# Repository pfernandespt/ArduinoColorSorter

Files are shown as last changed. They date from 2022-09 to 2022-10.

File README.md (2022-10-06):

# ArduinoColorSorter
## Introdução
Todo este trabalho tem origem no projeto a desenvolver proposto pelo professor da UC de Introdução à Engenharia Eletrotécnica.
Todos os diferentes projetos sugeridos tinham a sua base na plataforma Arduino com objetivos de trabalho diferentes.

Foi-nos proposto o desenvolvimento de um projeto que tivesse por base o controlo de posição e velocidade síncrono de 2 motores passo Nema17 usando drivers controladores L293D, contidos num módulo shield para um Arduino UNO.

Depois de alguma troca de ideias pensamos em fazer um dispositivo capaz de identificar a cor de um objeto e com base nisso separá-lo junto com outros de uma cor semelhante, ou seja, um separador de objetos por cor, uma vez que seria basicamente necessário adicionar um sensor de cor ao projeto. Decidimos adicionar também um botão para pausar/resumir o programa e uma fita de LEDs para uma fácil visualização da cor do objeto identificada pelo sensor.

Depois de alguma pesquisa percebemos que o uma boa opção seriam M&M’s: fáceis de obter, tendo 6 cores diferentes (vermelho, laranja, amarelo, verde, azul e castanho) e tamanhos semelhantes entre si.

O nosso projeto teve inspiração em alguns trabalhos anteriores que encontramos através de pesquisa na internet. O mais relevante terá sido um projeto completo desenvolvido por Willem Pennings muito bem documentado, com imagens e com projeto também no github:
 - [M&Ms and Skittles sorting machine](https://willempennings.nl/mms-and-skittles-sorting-machine/)
 - [Projeto GitHub](https://github.com/willem-pennings/Candy-sorting-machine)

## Material
  - 1 arduino
  - 1 módulo Adafruit Motor Shield;
  - 2 motores stepper/passo Nema 17;
  - 1 sensor de cor TCS34725 da DFRobot;
  - 1 fita de LEDs digital/endereçável de 1m, com 60LEDs/m;
  - 1 botão
  - x fios de ligação (jumpers)
  
## Hardware
  #### Esquema de Montagem (Schematic)
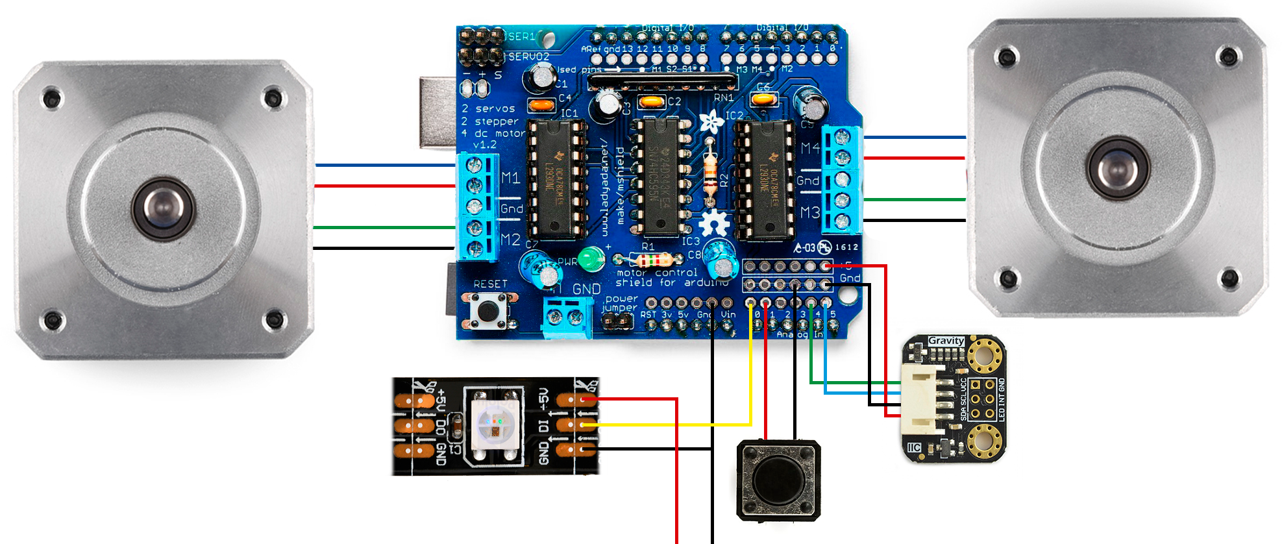
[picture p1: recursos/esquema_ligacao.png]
schematic
  
  
  #### Parte Mecânica
  Para facilitar o manuseamento dos M&M’s decidimos imprimir algumas peças em 3D:
  A peça amarela é da autoria de Willem Pennings retirada do projeto mencionado acima e as outras duas foram modeladas por nós no software Fusion 360.
  
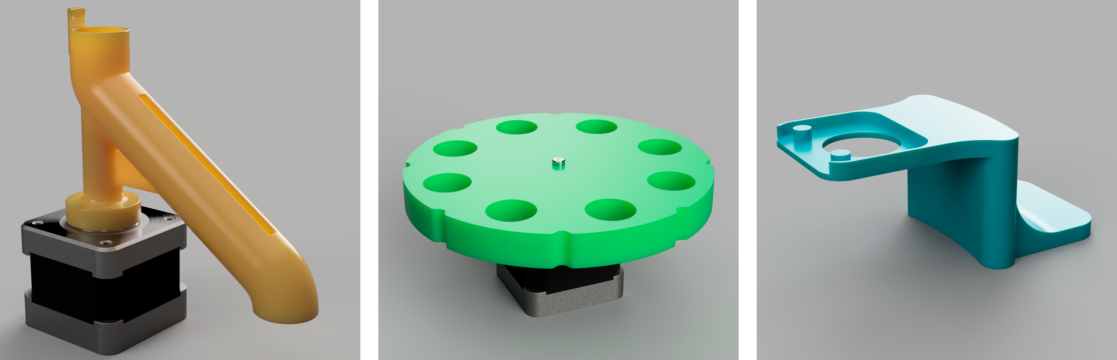
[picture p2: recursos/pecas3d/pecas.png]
pecas
  
  
  O motor com a peça amarela acoplada funciona como o próprio seletor do recipiente adequado, a verde é aquela que move os objetos sucessivamente até ao sensor e ao seletor (amarelo). Já a peça azul funciona como um suporte para o sensor de cor para que as leituras sejam mais consistentes à distância ideal.
  
  #### Prototipo Final
  
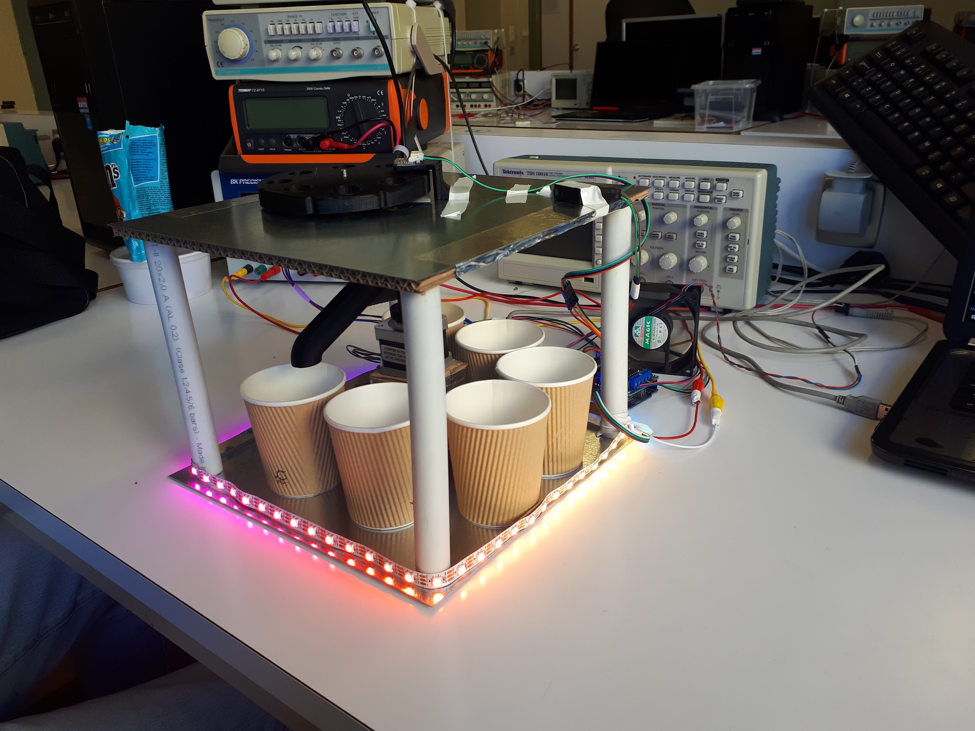
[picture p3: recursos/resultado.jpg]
prototype
  
  
  A ideia inicial era de fazer a estrutura redonda em MDF cortado a laser (como no modelo 3D), mas acabamos por fazer um modelo retangular de cartão e chapa galvanizada para lhe conferir resistência (acima).
  
## Software
#### Explicação
Todo o software foi desenvolvido e aperfeiçoado por nós, tendo tido por base algumas bibliotecas:
  - Wire.h (comunicação Arduino - Sensor Cor)
  - DFRobot_TCS34725.h (comunicação Arduino - Sensor Cor)
  - AFMotor.h (controlo dos motores stepper com o shield AdaFruit)
  - FastLED.h (controlo dos LEDs digitais)
Depois de procurar códigos de dispositivos como este online para inspiração decidimos desenvolver um método mais simples que aqueles que encontrámos na determinação da cor de cada objeto. 

Em vez de fazer comparações de cada um dos parâmetros R, G e B da cor lida pelo sensor com valores padrão pensamos no seguinte método:
  1. Construir pontos no espaço cujas coordenadas sejam os valores R,G e B das cores lida e
padrão (Ex: R:255 G:125 B:0 forma o ponto S de coordenadas (255, 125, 0));
  2. Calcular a distância entre o ponto correspondente à cor lida e cada um dos pontos
correspondentes aos valores padrão;
  3. Determinar a distância mínima das anteriores;
  4. Deduzir qual o ponto mais próximo ao lido e, como consequência, determinar a cor mais
próxima.

O processo descrito acima pode ser vizualizado com a ajuda do seguinte gráfico:
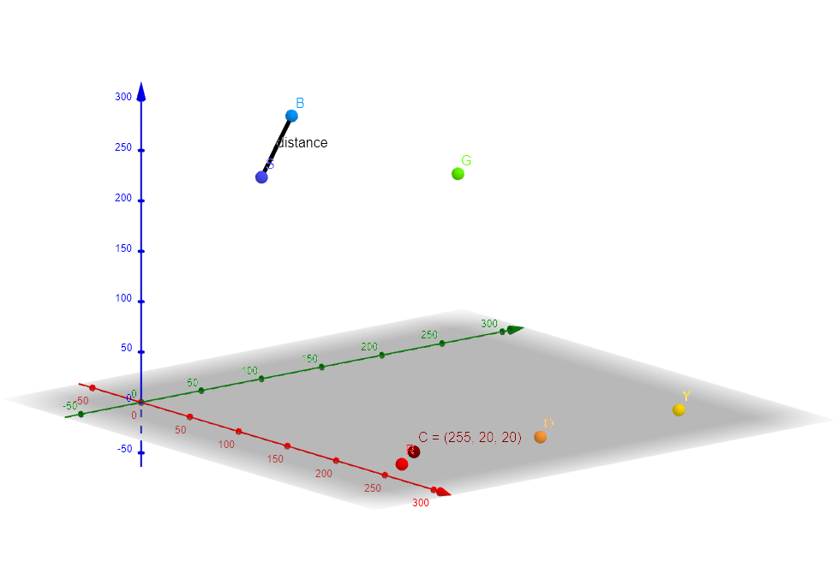
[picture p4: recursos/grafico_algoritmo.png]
explanation_diagram

Aqui é feita uma abstração dos eixos x, y e z aos valores R, G e B das cores lidas.

#### Código Responsável

Aproximação da cor:
```c
  int aprox_color(){ //devolve o numero da cor mais proxima a que foi lida no sensor
	int color_number = 0;
	float min_distance = distance(0);
  for(int i = 0; i < 7; ++i){
    float cur_distance = distance(i);
    if(cur_distance < min_distance){
      color_number = i;
      min_distance = cur_distance;
    }
  }
  return color_number;
}
```
```c
float distance(int i){ // calcula a distancia da cor lida a cor indicada no argumento
  float dist = sqrt(pow((r-cor[i].r),2) + pow((g-cor[i].g),2) + pow((b-cor[i].b),2));
  return dist;
}
```

Movimento dos motores:
```c
void move2(){
  int movement = abs(next_pos - last_pos);
  movement *= sector_amplitude;
  Serial.print("movimento motor baixo:");
  Serial.println(movement);
  if(next_pos > last_pos) {
    motor2.step(movement, FORWARD, DOUBLE);
    delay(100);
  }
  else {
    motor2.step(movement, BACKWARD, DOUBLE);
    delay(100);
  }
  
  last_pos = next_pos;
}
```

Para informação mais detalhada acerca deste projeto, por favor, consultar os documentos produzidos: [Relatório e Powerpoint](documentos)

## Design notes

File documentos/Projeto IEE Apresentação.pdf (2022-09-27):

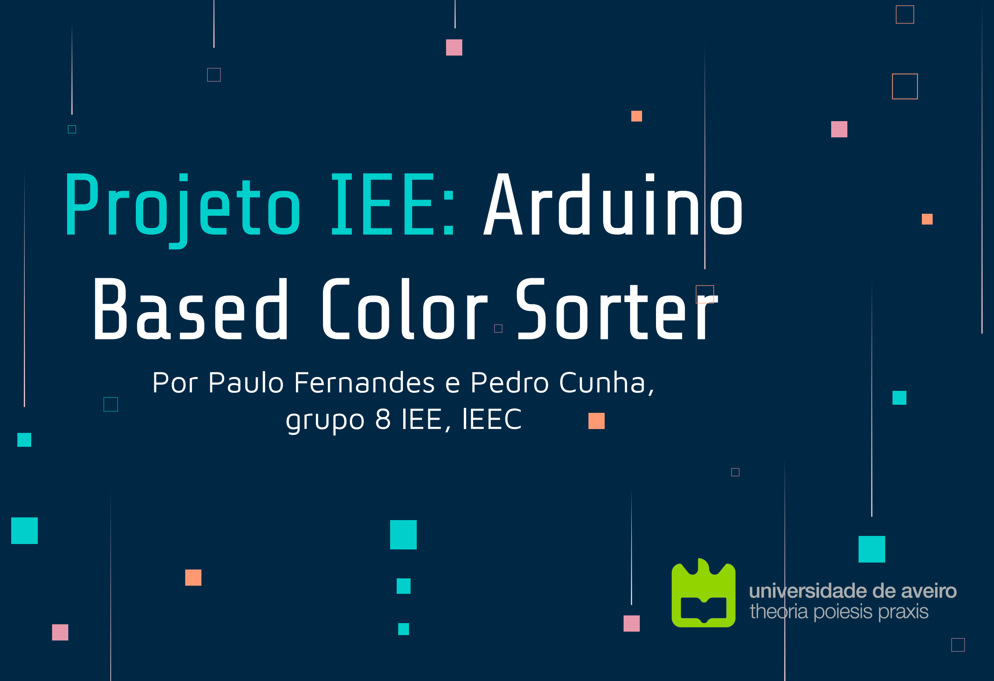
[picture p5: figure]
Por Paulo Fernandes e Pedro Cunha, grupo 8 IEE, lEEC; Projeto IEE: Arduino Based Color Sorter

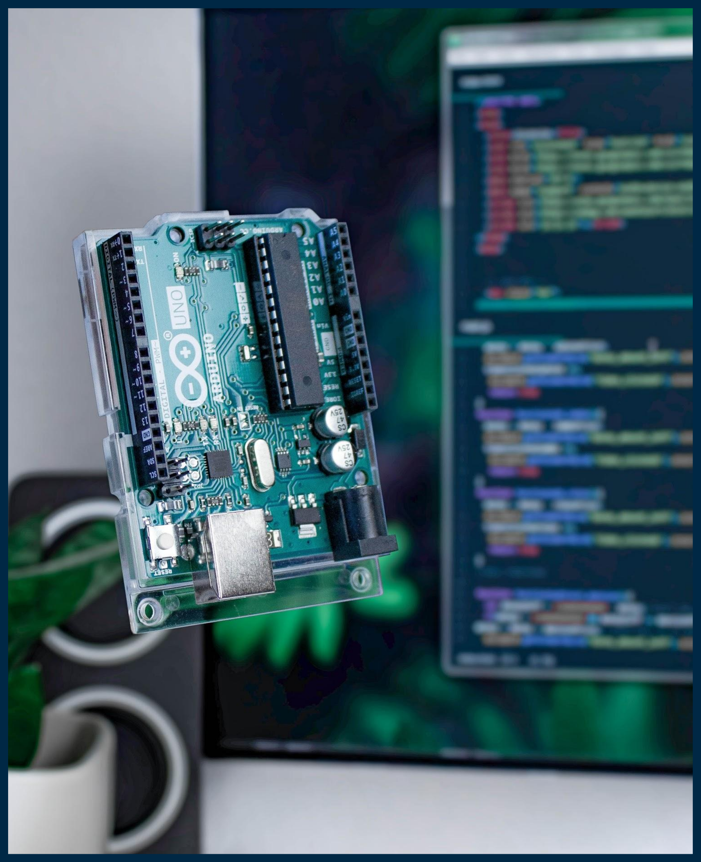
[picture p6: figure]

1. Plataforma Arduino;
2. Ideia base do Projeto;
3. Complementos;
4. Projeto como um todo;
5. Esquema de ligação;
6. Esquema de funcionamento;
7. Código;
8. Resultado;
9. Possíveis aplicações.

## Índice

O Arduino é uma plataforma open-source baseada em hardware e software de fácil manipulação. As placas Arduino são capazes de ler entradas e torná-las em saídas, seja através de sinais analógicos ou digitais. Tudo isto é feito através de uma linguagem de Programação baseada em C. (Adaptado de: What is Arduino?, arduino.cc) (https://www.arduino.cc/en/Guide/Introduction)

## Plataforma Arduino

Materiais Base:
■ 2 Motores stepper Nema17;
■ Adafruit Shield controlador de motores stepper para Arduino; ■ Arduino.

Objetivo: Desenvolvimento de um programa capaz de controlar velocidade e posição de motores stepper Nema17 aplicada a um trabalho e tendo por base os controladores L239D.

## Ideia Base do Projeto

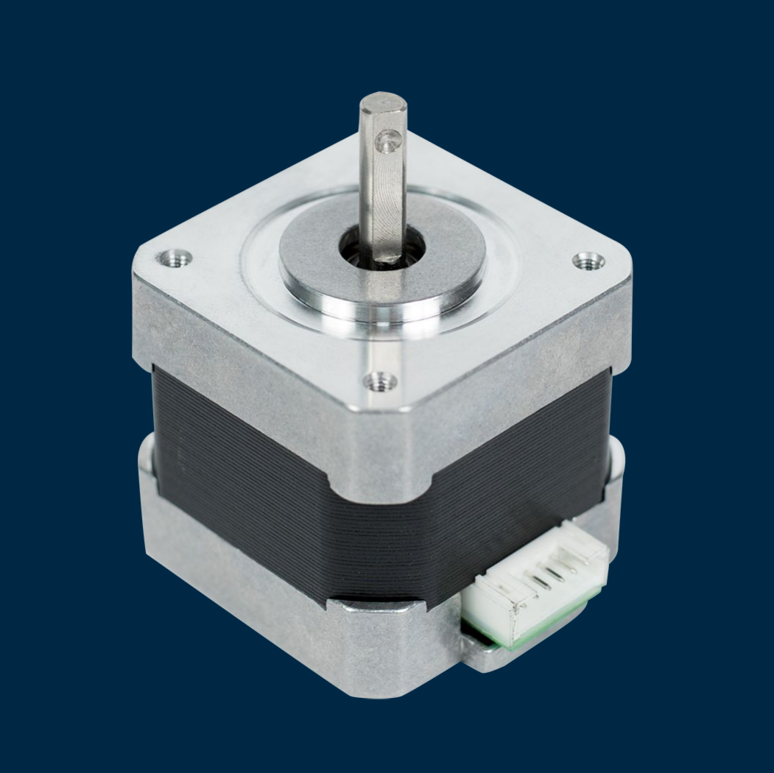
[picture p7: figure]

Desc.: Motor de passo bipolar

Características:
■ Número de fases: 2 (4 fios)
■ Passos por volta: 200
■ Ângulo de passo: 1.8º
■ Tensões de funcionamento: 5-12V

## Motores Stepper Nema17

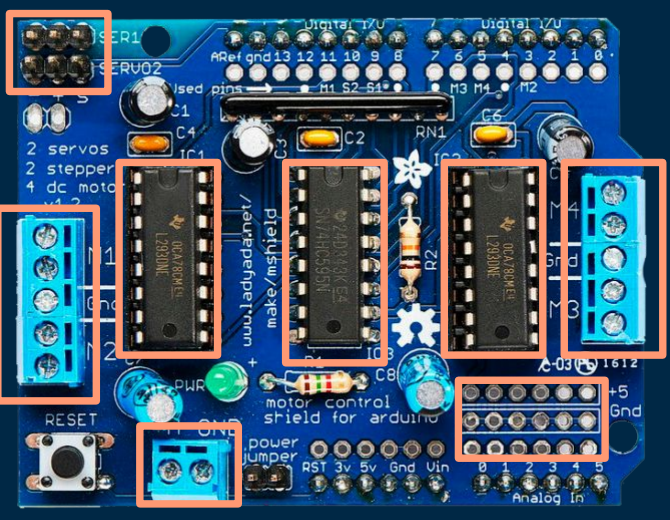
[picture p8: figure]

Desc.: “Shield” para Arduino que permite controlar diferentes tipos de motores (4 DC, 2 Stepper, 2 Servo).

Características:
■ 2 Drivers L293D
■ Fácil instalação no Arduino
■ Deixa livres as portas Analógicas do Arduino

## Adafruit Motor Shield

A nossa ideia de projeto implicou que fossem usados mais dispositivos eletrónicos:
■ Sensor de cor RGB DFRobot TCS34725
■ Fita de LEDs digital WS2812B 60LED/m
■ Botão Push
■ Jumpers

## Complementos

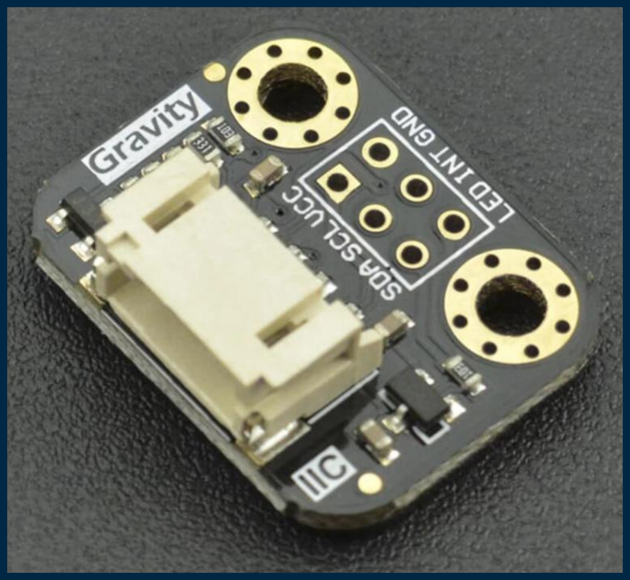
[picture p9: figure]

Desc.:Sensor de cor que permite obter os valores R, G e B de um objeto colocado na sua frente

Características:
■ Possui LEDs para melhor leitura ■ Padrão de comunicação: I2C ■ Usa apenas 2 Portas Analógicas

## Sensor de Cor RGB TCS34725

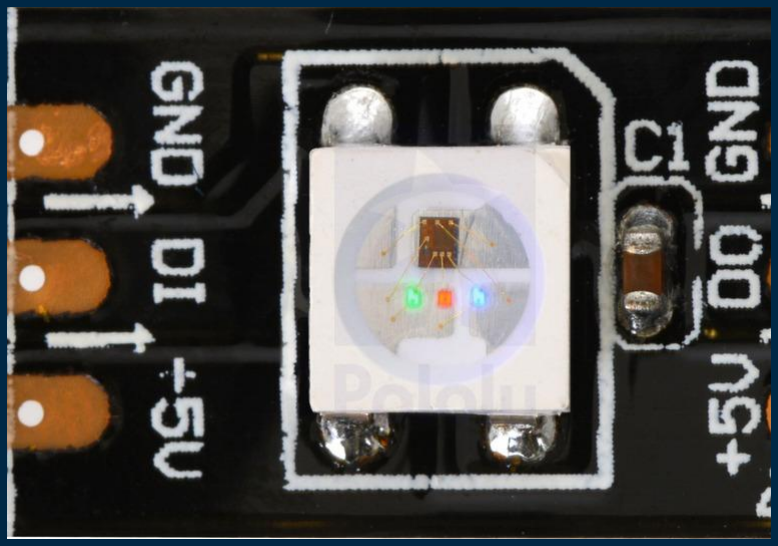
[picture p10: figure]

Desc.: Fita de LEDs endereçáveis de “baixo” consumo que exibe cores de 8 bits.

Características:
■ Potência máxima: 18W
■ Digital (controlo com 1 pino)

## Fita de LEDs WS2812B

Ideia principal do projeto: criação de um dispositivo capaz de separar objetos de cores diferentes.

Objeto a separar: M&M’s
■ Boa dimensão para fins demonstrativos
■ 6 cores: Vermelho, Laranja, Amarelo, Verde, Azul e Castanho ■ Tamanho consistente

## Projeto

## Projeto

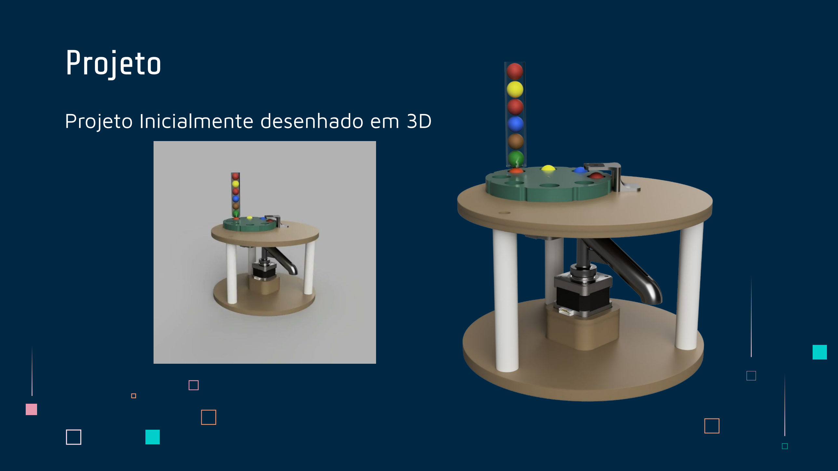
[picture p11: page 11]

Projeto Inicialmente desenhado em 3D

## Esquema de Ligação

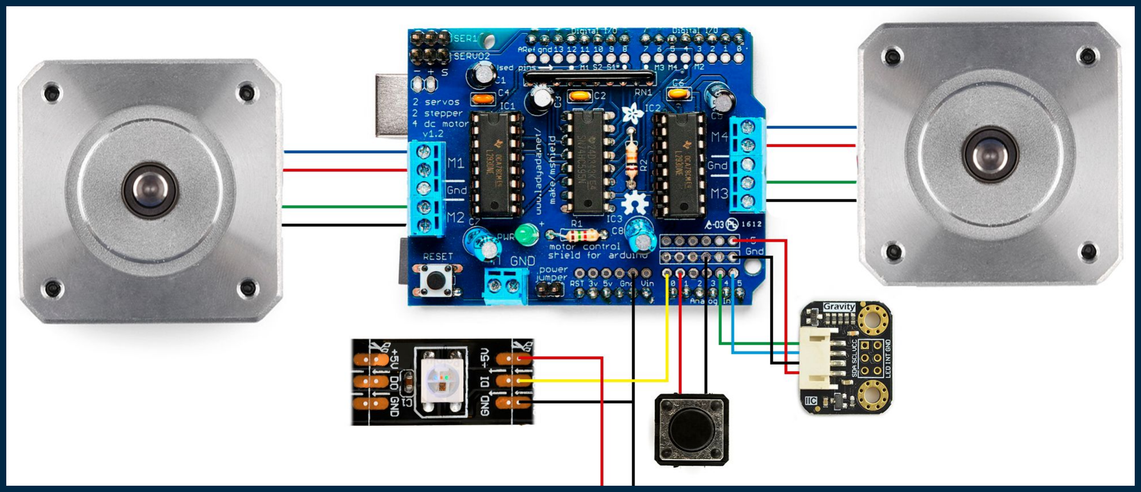
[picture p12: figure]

## Esquema de funcionamento

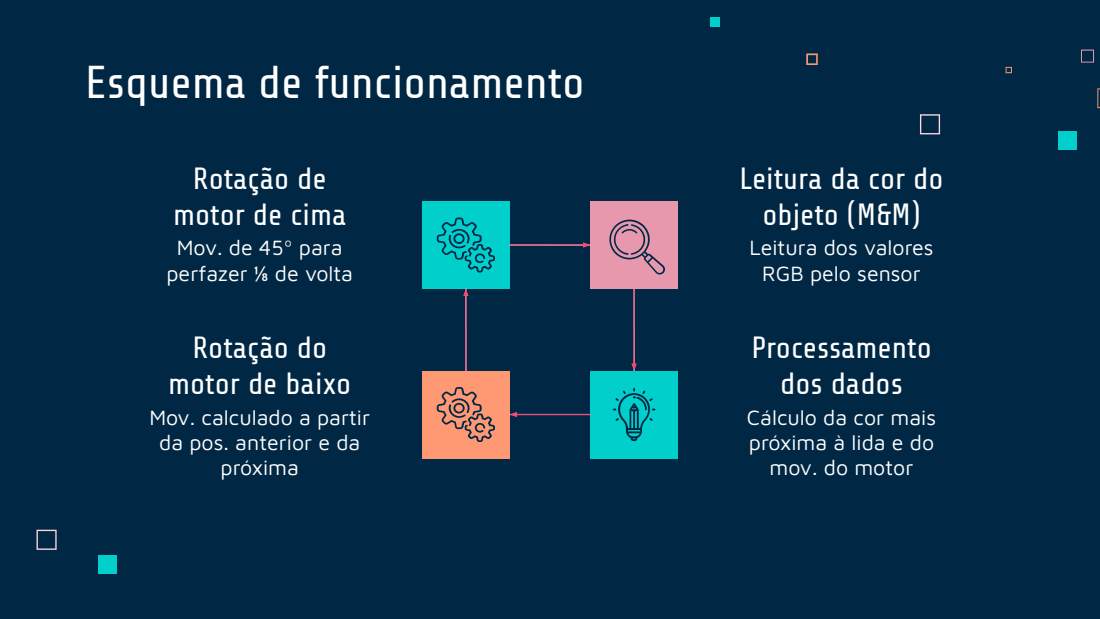
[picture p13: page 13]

Rotação de
motor de cima
Mov. de 45º para
perfazer ⅛ de volta

Leitura da cor do
objeto (M&M)
Leitura dos valores
RGB pelo sensor

Rotação do
motor de baixo
Mov. calculado a partir
da pos. anterior e da
próxima

Processamento
dos dados
Cálculo da cor mais
próxima à lida e do
mov. do motor

## Código (Processamento dos dados)

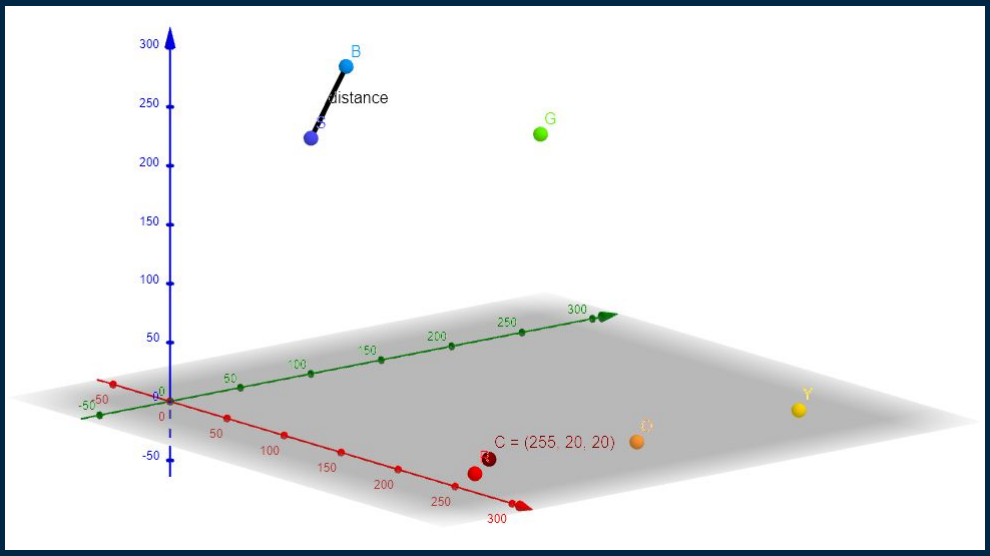
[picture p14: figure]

# Resultado

## Possíveis aplicações

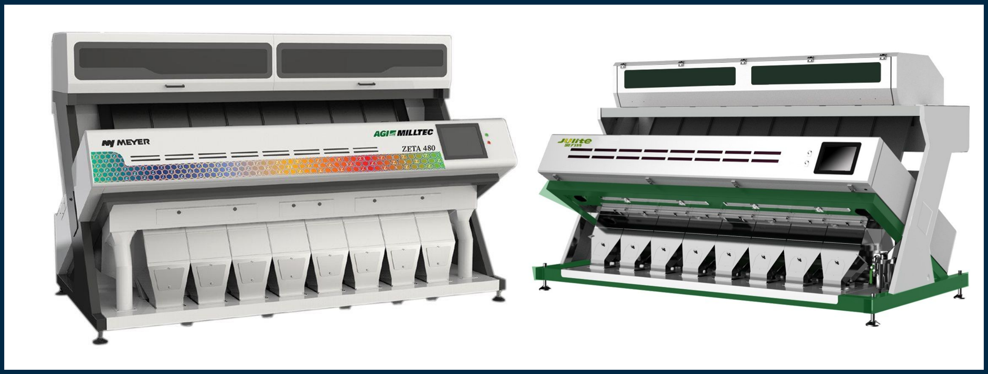
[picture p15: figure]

Indústria alimentícia no processamento de: ■ Milho
■ Feijão
■ Trigo
■ Sesamo
■ Arroz
■ Amendoins
■ Frutas

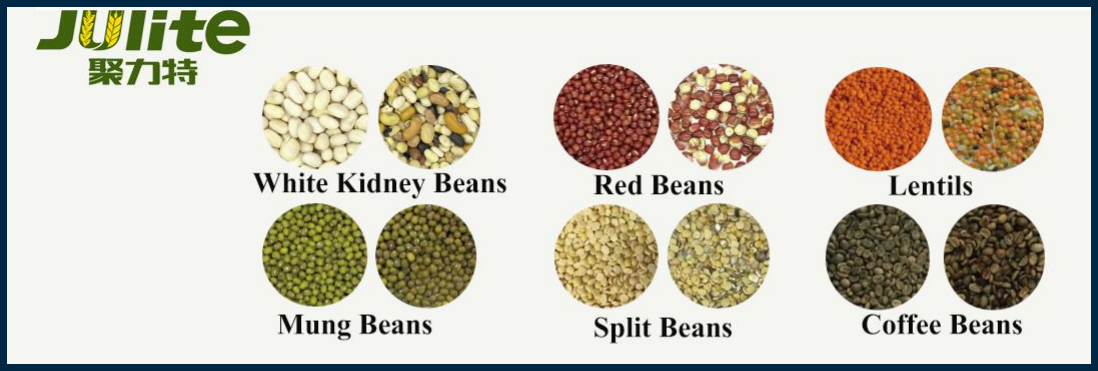
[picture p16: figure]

■ Sementes de Girassol
■ Outros…

## Possíveis aplicações

Separação de plásticos para reciclagem

## Possíveis aplicações

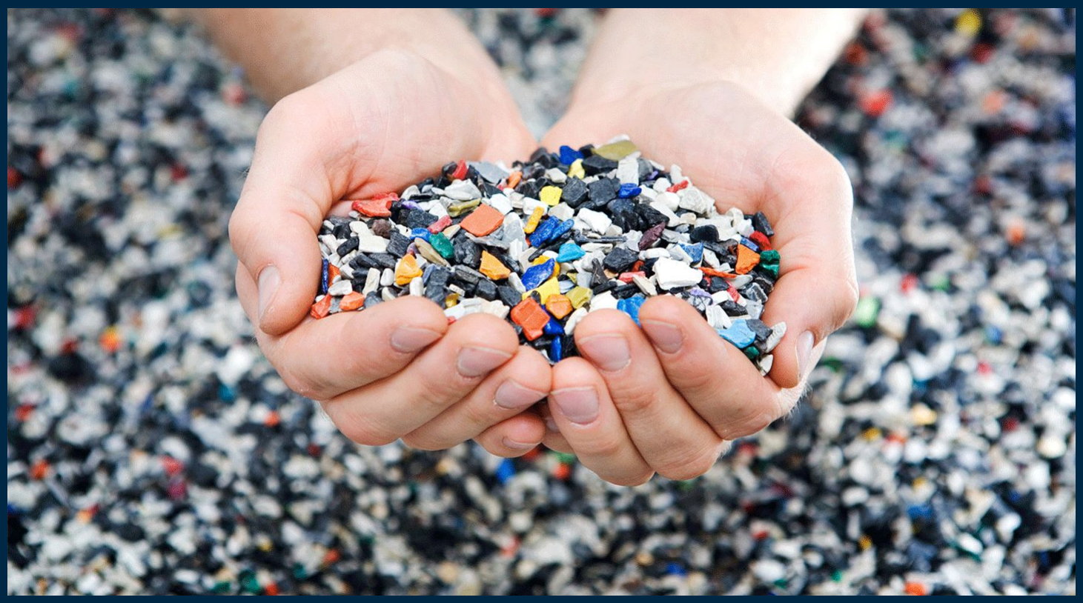
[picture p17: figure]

# Obrigado!

■ Arduino - What is Arduino (https://www.arduino.cc/en/Guide/Introduction)
■ LastMinuteEnginieers - Motor Shield (https://lastminuteengineers.com/l293d-motor-driver-shield-arduino-tutorial/)
■ CircuitBasics - Basics of the I2C communication protocol (https://www.circuitbasics.com/basics-of-the-i2c-communication-protocol/) ■ Julite - Color Sorter (https://www.julite.com/Product/id/236.html)

## Fontes

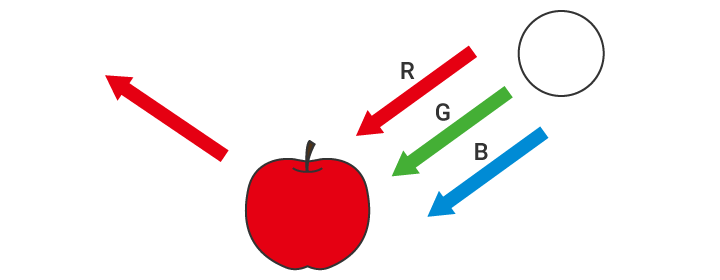
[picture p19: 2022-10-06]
recursos/sensor_cor1.png

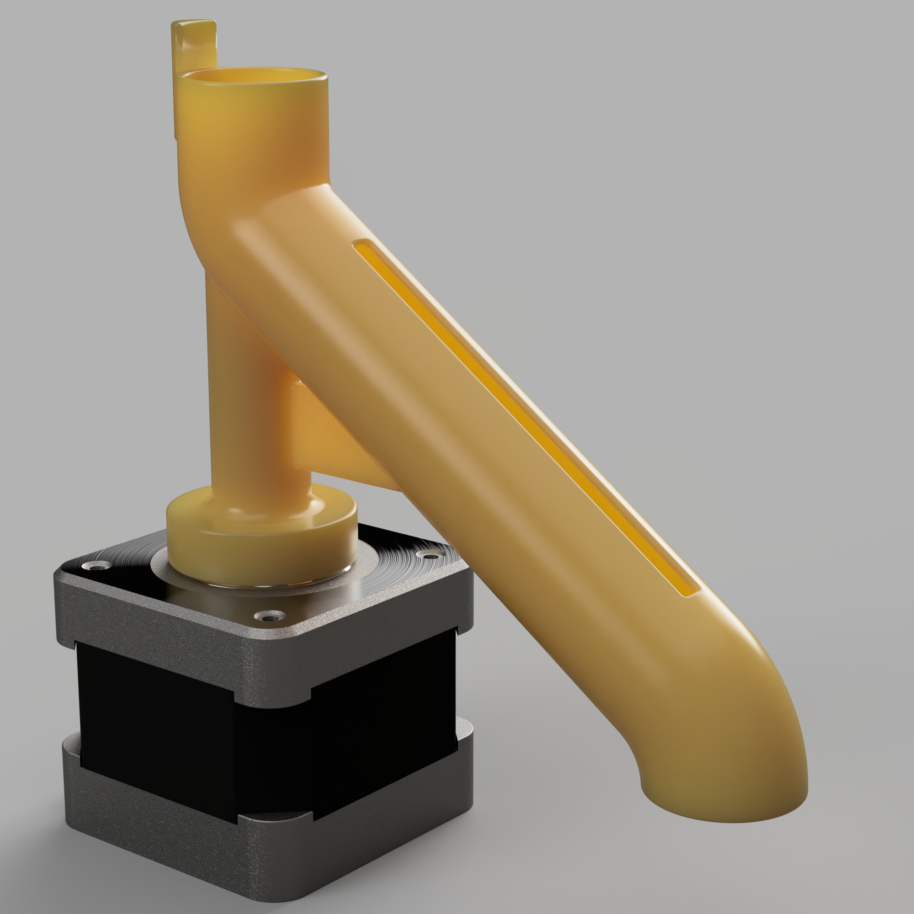
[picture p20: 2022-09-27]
recursos/pecas3d/peca1.png

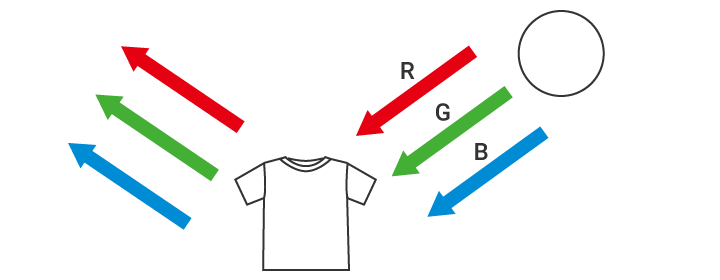
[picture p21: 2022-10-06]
recursos/sensor_cor2.png

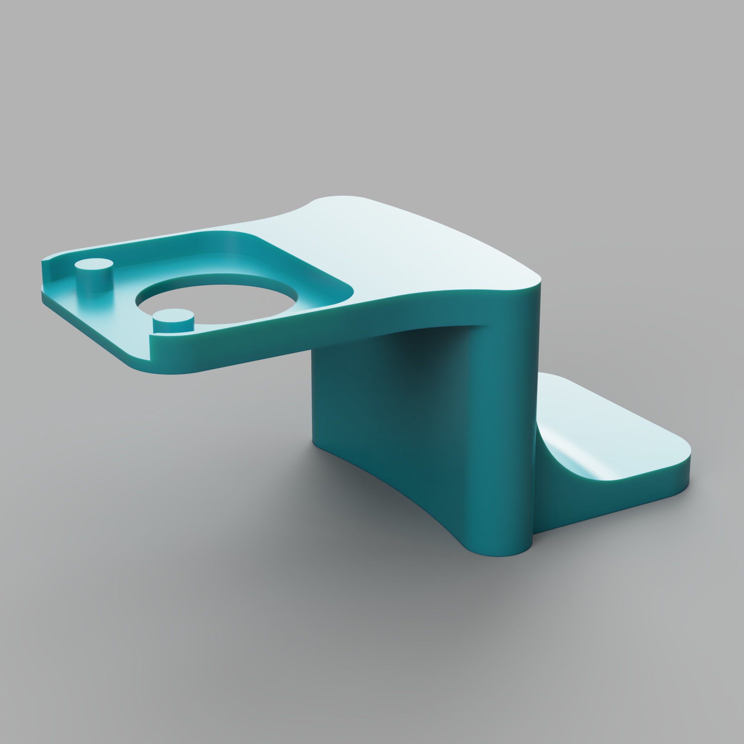
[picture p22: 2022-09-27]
recursos/pecas3d/peca3.png

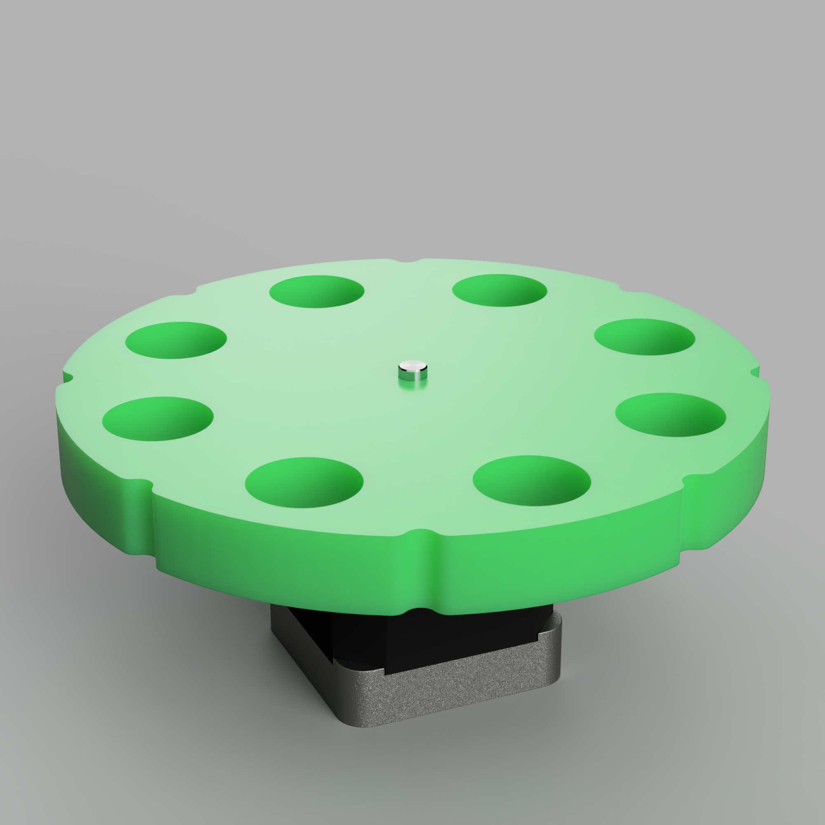
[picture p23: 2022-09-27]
recursos/pecas3d/peca2.png

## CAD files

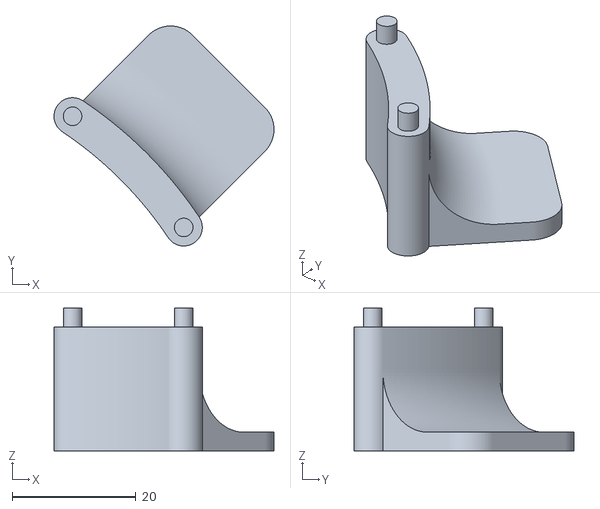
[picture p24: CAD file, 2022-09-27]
recursos/pecas3d/peca3-2.stl
35.5 x 35.5 x 23.0

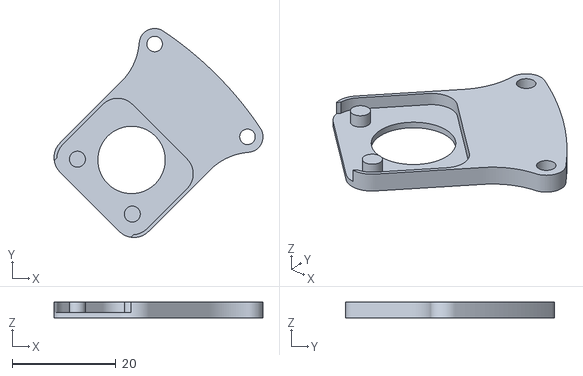
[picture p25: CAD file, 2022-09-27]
recursos/pecas3d/peca3-1.stl
40.4 x 40.4 x 3.00

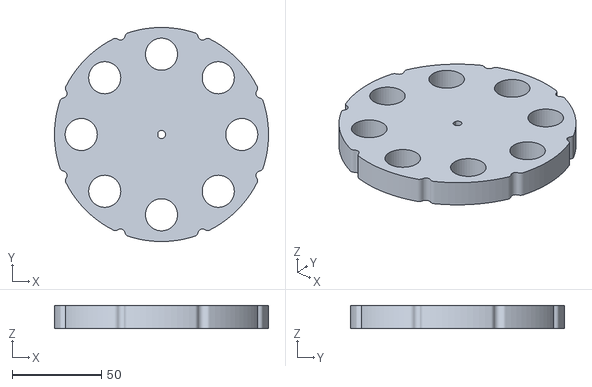
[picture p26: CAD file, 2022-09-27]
recursos/pecas3d/peca2.stl
119.9 x 119.9 x 13.0

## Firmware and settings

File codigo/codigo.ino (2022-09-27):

/*  
 *    Descrição: O seguinte codigo tem por objetivo através da utilização de um sensor de cor e de motores 
 *    stepper executar a separação de coisas de até 6 cores diferentes tendo por base valores padrão indicados.
 *    
 *    Universidade: UAveiro | Departamento: DETI | Curso: EEC | Ano: 2022 | Cadeira: IEE | Professor: Pedro Cabral
 *    Grupo nº8: Paulo Fernandes, Pedro Cunha
 */
 
//bibliotecas e variaveis para o sensor de cor //////////////////////////////////

#include <Wire.h>
#include "DFRobot_TCS34725.h"

uint16_t sensor_clear, sensor_red, sensor_green, sensor_blue;

/* Esquema de fios do sensor
 *  VERMELHO 5V
 *  PRETO GND
 *  AZUL SCL ou A5
 *  VERDE SDA ou A4
 */

DFRobot_TCS34725 tcs = DFRobot_TCS34725(TCS34725_INTEGRATIONTIME_50MS, TCS34725_GAIN_16X); //inicialização sensor de cor

//bibliotecas e variaveis para os motores stepper ///////////////////////////////
#include <AFMotor.h>
#define StepsPerRevolution1 200 //revoluções por volta motor 1 (cima)
#define StepsPerRevolution2 200 //revoluções por volta motor 2 (baixo)
#define Motor1Speed 50          //RPM maximo do motor 1
#define Motor2Speed 50          //RPM maximo do motor 2
#define Motor1Angle 45          //amplitude que o motor de cima tem que rodar para pegar mais um M&M
#define Motor2Freedom 300       //amplitude maxima que o motor2 pode rodar

AF_Stepper motor1(StepsPerRevolution1,2); //inicialização motor 1
AF_Stepper motor2(StepsPerRevolution2,1); //inicialização motor 2

int last_pos = 1, next_pos;
const int rotation_step = map(Motor1Angle,0,360,0,StepsPerRevolution1);
//const int rotation_step = 25;
const float  sector_amplitude = map(Motor2Freedom, 0, 360, 0, StepsPerRevolution2)/ 6;

//bibliotecas e variaveis para os leds endereçaveis /////////////////////////////
#include <FastLED.h>
#define NumLeds 60 //numero de leds da fita 
#define LedsPin A0 //pino onde a fita esta ligada
#define Brightness 255 //brilho dos leds 0 - 255

CRGB leds[NumLeds];
CRGBPalette16 Palette = RainbowColors_p;
//CRGBPalette16 Palette; //palete de cores para quando o programa está em pausa
byte StartIndex = 0;

//Processamento dos dados //////////////////////////////////////////////////////
byte r,g,b, max_color, min_color, nearest_color; //processamento das cores para ficarem mais vivas

struct color{  
  byte r;
  byte g;
  byte b;
  byte pos; //posição no recipiente
  char c;   //letra representativa
};

const color cor[7] = { //cores padrao para a comparacao
  {255,255,255, 0, 'N'}, //nada detetado
  {255, 10, 10, 1, 'R'}, //cor 1
  {255,125, 10, 2, 'O'}, //cor 2
  {255,243, 10, 3, 'Y'}, //cor 3
  { 10,255,170, 4, 'G'}, //cor 4
  {  0,125,255, 5, 'B'}, //cor 5
  {255, 20, 20, 6, 'C'}  //cor 6
  };

int contador[7];

//Controlo /////////////////////////////////////////////////////////////////////
#define Button A1

void setup() { /////////////////////////////////////////////////////////////////
  pinMode(Button, INPUT_PULLUP);
  
  Serial.begin(9600);
  Serial.println("Comunicacao Serie Inicializada!");

  Serial.print("Motors:  M1: ");
  Serial.print(sector_amplitude);
  Serial.print("   M2: ");
  Serial.println(rotation_step);
  
  motor1.setSpeed(Motor1Speed);
  motor2.setSpeed(Motor2Speed);

  for(int i = 0; i < 7; ++i) contador[i] = 0; //inicializa o contador de cores a 0;

  FastLED.addLeds<WS2812B, LedsPin, GRB>(leds, NumLeds); //inicialização da fita de leds
  FastLED.setBrightness(Brightness);
  /*Palette[0] = CRGB::White;
  Palette[1] = CRGB::White;
  Palette[2] = CRGB::White;
  Palette[3] = CRGB::White;
*/
  if(tcs.begin()){ //tentar encontrar o sensor de cor no I2C
    Serial.println("Sensor de Cor encontrado!");
  } else {
    Serial.println("Erro! Sensor de Cor desconectado!");
    while(true); //se ocorrer um erro a encotrar o sensor o programa para a execução
  }

  Serial.println("Tubo Seletor na Primeira posicao? Confirme..."); //Para que o programa saiba sempre em que posição se encontra o motor
  while(digitalRead(Button) == HIGH){
    leds_pause(StartIndex);
    StartIndex += 1;
    delay(10);
  }
  Serial.println("Tudo Certo! Iniciando Programa!");
  while(digitalRead(Button) == LOW);
}

void loop() { /////////////////////////////////////////////////////////////////
  
  //ação do motor1
  motor1.step(rotation_step, BACKWARD, DOUBLE);
  delay(500);
  //ação do sensor de cor
  tcs.getRGBC(&sensor_red, &sensor_green, &sensor_blue, &sensor_clear); //leitura da cor do sensor
  tcs.lock();
  
  r = sensor_red   * 255.0/sensor_clear; //Calculo dos Valores R na gama 0-255
  g = sensor_green * 255.0/sensor_clear; //Calculo dos Valores G na gama 0-255
  b = sensor_blue  * 255.0/sensor_clear; //Calculo dos Valores B na gama 0-255

  Serial.print("Original: ("); 
  Serial.print(r);
  Serial.print(';');
  Serial.print(g);
  Serial.print(';');
  Serial.print(b);
  Serial.print(") -> Processado: (");

  // processamento dos valores para obter cores mais vivas
  max_color = max(max(r,g),b);
  min_color = min(min(r,g),b);

  if(abs(r - min_color) <= 10) r *= 0.1;
  if(abs(g - min_color) <= 10) g *= 0.1;
  if(abs(b - min_color) <= 10) b *= 0.1;

  r = map(r, 0, max_color, 0, 255);
  g = map(g, 0, max_color, 0, 255);
  b = map(b, 0, max_color, 0, 255);

  nearest_color = aprox_color(); //chama a funcao
  
  Serial.print(r);
  Serial.print(';');
  Serial.print(g);
  Serial.print(';');
  Serial.print(b);
  Serial.print(") Nearest color is ");
  Serial.println(cor[nearest_color].c);
  
  contador[nearest_color]++; //incrementa o contador de mm's
  
  for(int i = 1; i < 7; ++i){ //Imprime a contagem de MMs de cada cor que já passaram pelo contador a cada iteracao
    Serial.print(cor[i].c);
    Serial.print(": ");
    Serial.print(contador[i]);
    Serial.print("   ");
  }
  
  //transmisao dos dados de cor para a fita de leds

  for(int i = 0; i < NumLeds; ++i){
    leds[i] = CRGB(r,g,b);
  }
  FastLED.show();

  //ação do motor2
  delay(500);
  next_pos = cor[nearest_color].pos;
  move2();

  delay(2000);
  //opcao de parar o programa 
  if_pause();

  
}
//funções necessarias //////////////////////////////////////////////////////////////////////////

int aprox_color(){ //devolve o numero da cor mais proxima a que foi lida no sensor
	int color_number = 0;
	float min_distance = distance(0);
  for(int i = 0; i < 7; ++i){
    float cur_distance = distance(i);
    if(cur_distance < min_distance){
      color_number = i;
      min_distance = cur_distance;
    }
  }
  return color_number;
}

float distance(int i){ // calcula a distancia da cor lida a cor indicada no argumento
  float dist = sqrt(pow((r-cor[i].r),2) + pow((g-cor[i].g),2) + pow((b-cor[i].b),2));
  return dist;
}

void move2(){
  int movement = abs(next_pos - last_pos);
  movement *= sector_amplitude;
  Serial.print("movimento motor baixo:");
  Serial.println(movement);
  if(next_pos > last_pos) {
    motor2.step(movement, FORWARD, DOUBLE);
    delay(100);
  }
  else {
    motor2.step(movement, BACKWARD, DOUBLE);
    delay(100);
  }
  
  last_pos = next_pos;
}

void if_pause(){
  if(digitalRead(Button) == LOW){
    Serial.println("Programa em Pausa! Para retomar clique novamente no botao!");

    next_pos = 1;
    move2();
    while(digitalRead(Button) == LOW);
    while(true){
      leds_pause(StartIndex);
      StartIndex += 1;
      delay(10);
      if(digitalRead(Button) == LOW) break;
    }
    Serial.println("Programa sera retomado! Por favor largue o botao.");
    while(digitalRead(Button) == LOW) delay(100);
  }
}

void leds_pause(byte f_index){
  int colorIndex = f_index;
  for( int i = 0; i < NumLeds; ++i) {
     leds[i] = ColorFromPalette(Palette, colorIndex, Brightness, LINEARBLEND);
     colorIndex += 3;
  }
  FastLED.show();
  
}

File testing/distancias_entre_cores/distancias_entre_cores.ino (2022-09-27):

int r,g,b;

struct color{  
  int r;
  int g;
  int b;
  char name[8];
};

const color cor[7] = {
  {255,255,255, "nada"},
  {255,0  ,  0, "vermelho"}, //cor 1
  {0  ,255  ,  255, "laranja"},  //cor 2
  {255  ,  255,  0, "amarelo"},  //cor 3
  {0  ,255,  0, "verde"},    //cor 4
  {0  ,  0,255, "azul"},     //cor 5
  {0  ,  0,  0, "castanho"}  //cor 6
  };
int nearest_color = 0;

float distance(const int i){ // calcula a distancia de byte r,g,b a cor indicada no argumento
  float dist = sqrt(pow((r-cor[i].r),2) + pow((g-cor[i].g),2) + pow((b-cor[i].b),2));
  return dist;
}

void setup() {
  Serial.begin(9600);
}

void loop() {
  r = 255;
  g = 10;
  b = 50;
  
  float min_dist = distance(0), cur_dist;
  for(int i = 0; i < 7;++i){
    cur_dist = distance(i);
    if(min_dist > cur_dist){
      nearest_color = i;
      min_dist = cur_dist;
    }
  }
  Serial.println(cor[nearest_color].name);
  while(1);
}

//funções necessarias //////////////////////////////////////////////////////////////////////////

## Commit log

2022-09-27 testes de diferentes componentes do projeto
2022-09-27 media produzida no decorrer do projeto
    [peca2.stl, peca3-1.stl, peca3-2.stl]
